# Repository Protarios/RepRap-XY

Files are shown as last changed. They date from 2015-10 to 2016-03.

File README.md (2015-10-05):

This is the first release of a RepRap-XY 3D printer. 
It is based on the great work of jand1122, which again is based on the excellent design of Zelogik. See the github archives at:  https://github.com/jand1122/RepRap-XY and https://github.com/zelogik/AluXY
I also use some of the parts parts clintonsam25 shared on the FreeCAD Forum and Github: https://github.com/clintonsam75/FreeCAD-library/tree/master/3D%20Printer and http://forum.freecadweb.org/viewtopic.php?f=24&t=6962

These designs and variants are discussed in the RepRap forum at:: http://forums.reprap.org/read.php?4,297740

jand1122 already changed the original design of zeologic so no more CNC-ed aluminium is needed. Based on this design he used printed parts instead of aluminium parts. 

The resulting design already has a great lot of features:

- Based on the Core-XY system. (see http://corexy.com/theory.html)
- Frame made from aluminium extrusions.
- No motors, belts and guides on the outside of the frame.

When thinking about the ideal FDM 3D printer I want to build those requirements come into my mind:

- Stiff Frame (check, aluminium extrusion profiles are great)
- High quality hotend (E3D or Kraken Printhead can be mounted, upgradeable)
- No Oozing Nozzle (Direct Feed or Closing Nozzle, like cel-robox has)
- Heated Bed for warp-free printing of ABS
- good first layer (automatic bed leveling, good sticking of layer to bed: Kapton Tape, PEI or GeckoTek)
- Capable of wide variety of materials
- Enclosed casing for warp and smell free printing (good starting point with jand1122's design, where no motors are outside the frame)
- Remote control with webcam support (Octopi)
- Multi Nozzle Printhead (higher printspeed, multi material / color prints)
- Swapable Head if possible

With the goal of adding such new features, like ocotopi webcam support, enclosed  caseing, dual nozzle printhead and others I decided to use jand1122s design as a basis for me own redesign.

I started with redesigning his FreeCAD parts, so screws are integrated in a nicer way and remodelling other parts in FreeCAD only available as STEP before.

Also I assemble the printer in the Freecad Assembly2 Module.

This is a work in progress, Use at your own risk.

The Folder src containes the FreeCAD files from jand1122 and from other open source 3D printer projects I used as basis for my design.

The Folder Assembly contains the FreeCAD Assembly and all Parts.
As the Assembly2 Module currently does not allow for import of subgroups of parts and the solver isn't able anymore to solve all constraints if the assembly gets to complicated I use the muxing ability of Assembly2 to join subgroups of parts, such as the XY-Slide into one part then used for further assembly in the complete product.

The file build.py will generate the STEP and STL files.
Just open the file in FreeCAD and run a a macro.

In the doc folder you will find a BOM. 
This BOM currently is fully based on jand1122's design. I will update it later.
This BOM is not generated from the model but hand made, so be carefull
You will not (yet?) find build instructions there.  Have a look at the sourcefiles RepRap-XY.FCStd (FreeCAD) to see how everything fits together.

To see some videos of jand1122's printer have a look at his youtube channel: https://www.youtube.com/channel/UCOyTdQOCCLdy45FtSlam_3A/feed
and some images at his imgur album: http://jand1122.imgur.com/

As I first want to complete the printer in CAD before I start any real life assembly it will be sone time until I can sho you videos or pictures of mine.

Have fun.

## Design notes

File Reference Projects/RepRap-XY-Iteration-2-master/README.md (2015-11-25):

# RepRap-XY-Iteration-2
## Open Source CoreXY RepRap 3D Printer
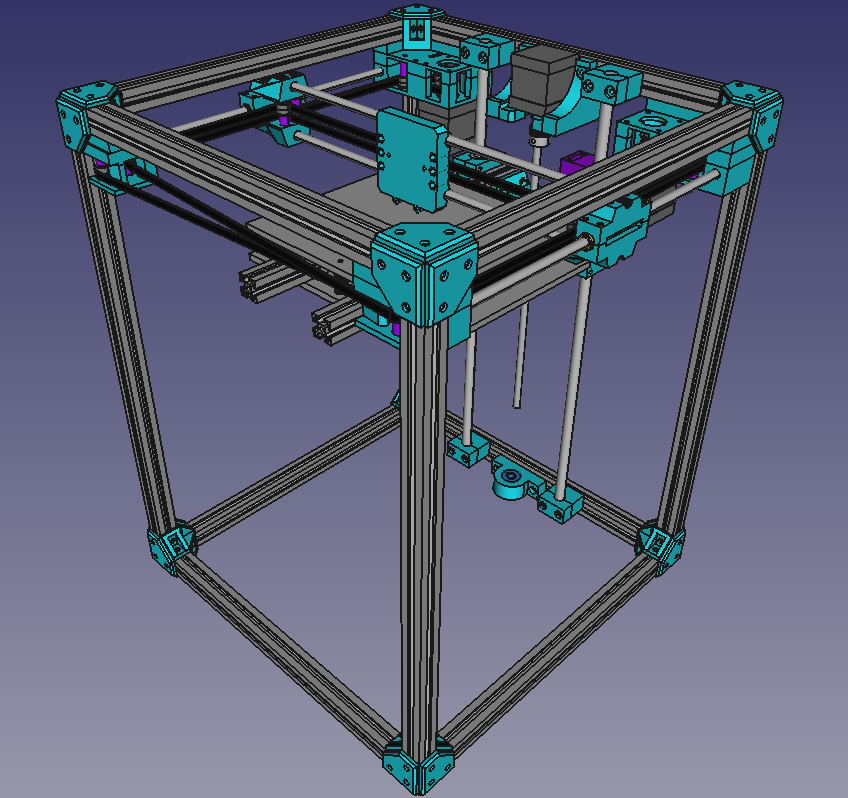
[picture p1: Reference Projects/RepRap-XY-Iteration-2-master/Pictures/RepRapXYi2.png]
RepRap-XY Iteration 2 Assembly

 RepRap-XY Iteration 2 FreeCAD Assembly

This is a modified release of the RepRap-XY 3D printer. It is based on the excellent design of Jand archive at:https://github.com/jand1122/RepRap-XY

Their designs/variants are discussed in the RepRap forum at:: http://forums.reprap.org/read.php?4,297740

RepRap-XY-Iteration 2 is designed to be an improvement over the original RepRap-XY design provided by Jand1122. Iteration 2 incorporated a modified X carriage and XY blocks from sdavi and incorporates 2020 coner brackets inspired by user ybm.

Iteration 2 Modifications:
- Sdavi's XY Blocks modified for 8x12x30 Brash Bushings
- Custom X Carriage based on Sdavi's design remodeled from scratch
- Mounting for E3D V6, E3D Chimera, E3D Cyclops 
- Increased Z axis height of 100mm, printer height 500mm
- Corner bracket parts for frame in lieu of metal right angle t-slot brackets
- Spacer corner brackets for motor blocks and idler blocks, also add structur to frame
- (x2) B'Struder Direct Driver Extruder w/ MK8 Driver Gear setup for 1.75mm Filament
- Mounting for Ultimachine RAMBo/AMBIT

## Bill of Materials

Frame
- (4x) 500mm 20x20 Length of Aluminum Extrusion
- (12x) 260mm 20x20 Length of Aluminum Extrusion
- Lots of M4 T-nuts
- (24x) Printed Corner Brackets
- (4x) Printed Inner Corner Brackets

Z Axis
- (2x) 12mm Rod 500mm
- Trapizoidal Lead Screw
- 5X10 Motor Coupler
- (2x) LM12LUU 12mm Long Linear Bearing
- Nema17 Stepper Motor
- (4x) M4 T-nuts
- (2x) 100mm 20x20 Aluminum Extrustion Length
- 14x 40mm M5 bolt
- (8x) 25mm M5 bolt
- (4x) 15mm M3 bolt (to attach nema motor)

X & Y Axis
- (2x) NEMA17 Stepper Motors
- (24x) F624ZZ flanged bearings
- (2x) 330-350mm 8mm diameter smooth rod (y-axis)
- (2x) 400mm 8mm diameter smooth rod (x-axis)
- (6x) LM8UU 8mm linear bearing
- Approx. 3-4m GT2 belt
- (2x) 20 tooth GT2 Pulley
- (4x) 60mm M4 bolts (for XY block bearings)
- (40x) M4 bolts
- (12x) 40mm M3 bolts
- (8x) 40mm M4 bolts (for idler bearings, screws can be longer)
- (8x) 25mm M5 bolts
- (6x) 55mm M5 bolts
- (4x) 30mm M5 bolts
- (6x) 15mm M3 bolt
- (8x) 10mm M3 bolt (attach nema motors)

Liscensing: 
Creative Commons Attribution-ShareAlike 4.0 International License

https://creativecommons.org/licenses/by-sa/4.0/legalcode

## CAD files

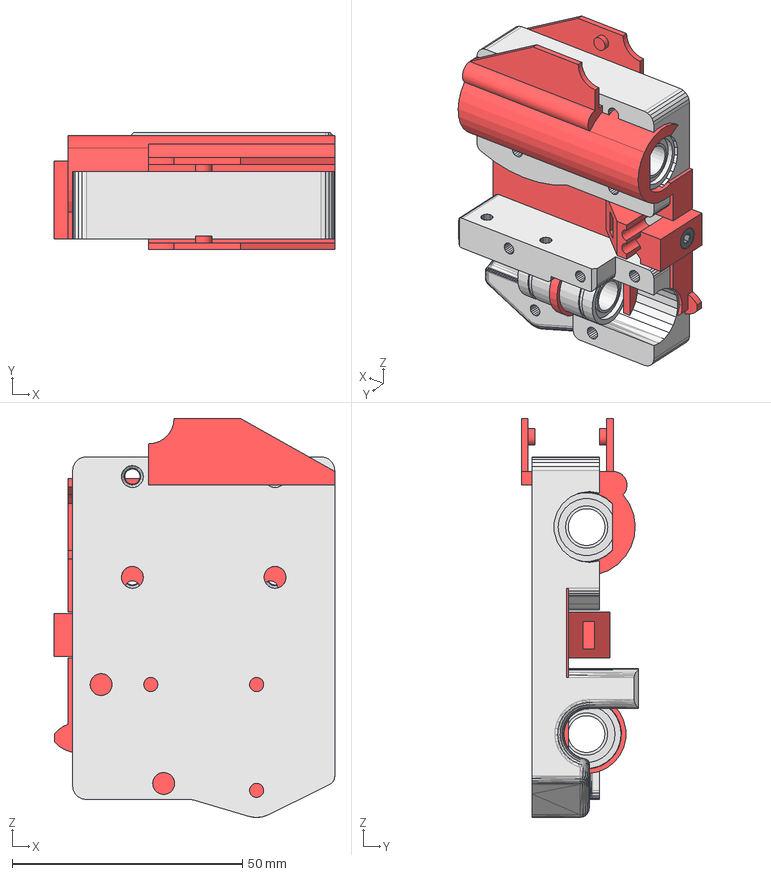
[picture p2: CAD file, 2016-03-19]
Assembly/Parts/Extruder/Toronado-Carrier-Assembly.FCStd
61.0 x 25.5 x 86.7 mm
x-carriage-final
x-LM8uu-top-1
x-LM8uu-top-002
x-LM8uu-bottom-003
x-carriage-zip-tie
x-carriage-B-final
M3-nut
M3x20-hex-bolt002
tpge_xcarriage002

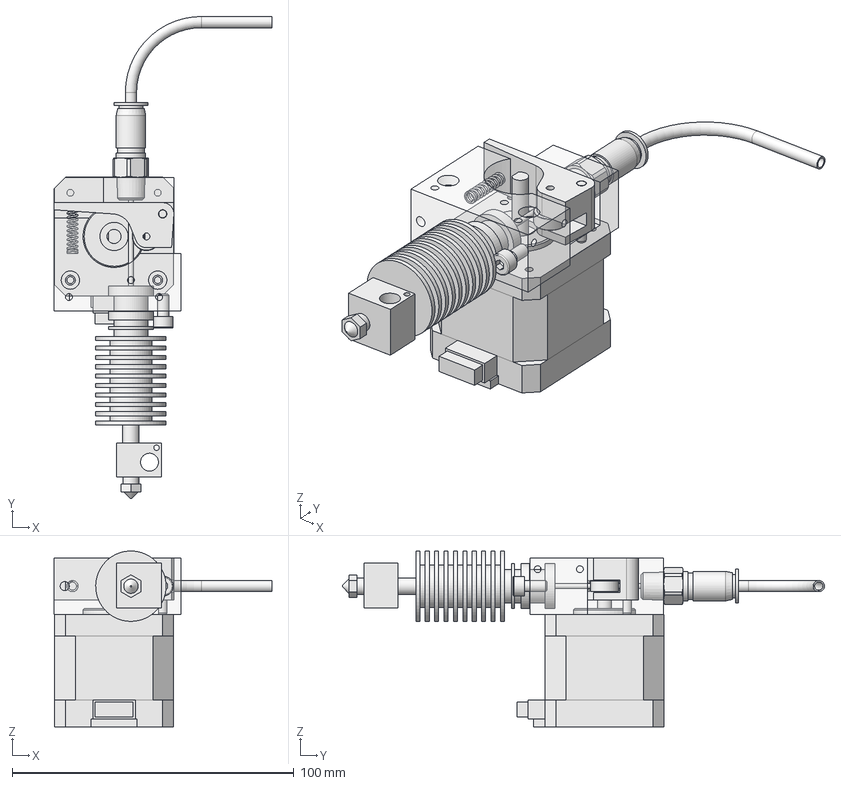
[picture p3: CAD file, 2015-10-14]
Assembly/Sub-Assemblies/extruder-assembly.FCStd
77.3 x 171.1 x 62.5 mm
C04H020019-extruder-spring
C04H030096-extruder-motor-support
C04H030009-Extruder-lever
Extruder_tube-end
C04H040001-pneumatic-fitting
C04H020008-Bearing-623zz
Extruder-body-bolt-2
hot-end-PLA-filament
C04H010011-extruder-motor
C04H050004-dowel-pin
hotend final001

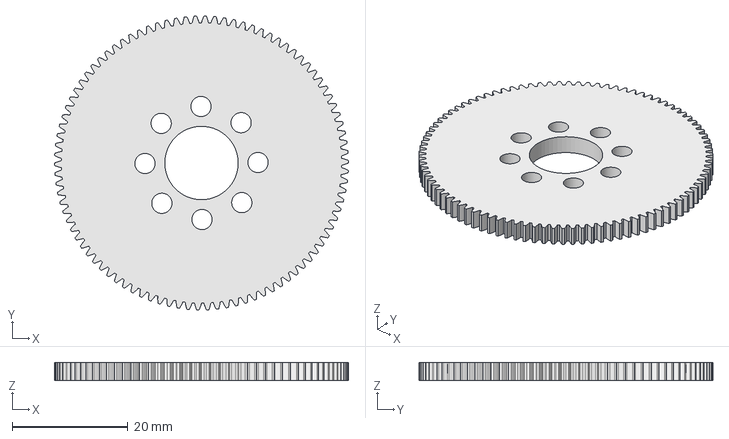
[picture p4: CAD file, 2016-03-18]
Assembly/Sub-Assemblies/Muxed Assemblies/The_Toranado_Precision_Geared_1.75mm_Extruder/files/Acetal Main Gear.FCStd
50.9 x 50.9 x 3.17 mm

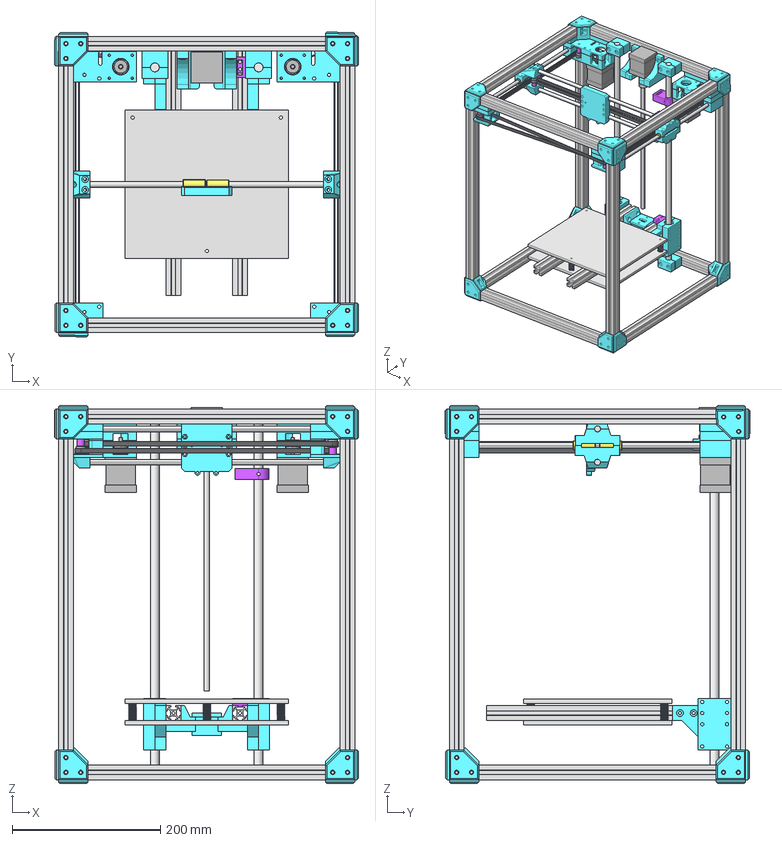
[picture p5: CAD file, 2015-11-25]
Reference Projects/RepRap-XY-Iteration-2-master/src/RepRap-XY-Iteration-2-Assembly.fcstd
410.7 x 411.3 x 510.0 mm
Nema-17
Nema-018
Nema-019
F624zz-bearing
624-bearing
spacer-1
F624zz-bearing001
624-bearing001
washer-M4
washer-M005
F624zz-bearing002
624-bearing002
washer-M006
washer-M007
F624zz-bearing003
624-bearing003
washer-M008
washer-M009
F624zz-bearing004
624-bearing004
washer-M010
washer-M011
washer-M012
washer-M013
F624zz-bearing005
624-bearing005
spacer-002
washer-M014
washer-M015
F624zz-bearing006
624-bearing006
spacer-003
washer-M016
washer-M017
F624zz-bearing007
624-bearing007
spacer-004
washer-M018
washer-M019
F624zz-bearing008
624-bearing008
washer-M020
washer-M021
F624zz-bearing009
624-bearing009
washer-M022
washer-M023
F624zz-bearing010
624-bearing010
washer-M024
washer-M025
F624zz-bearing011
624-bearing011
washer-M026
washer-M027
Alu-20x20x360
Alu-20x20x361
Alu-20x20x362
Alu-20x20x363
Alu-20x20x367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

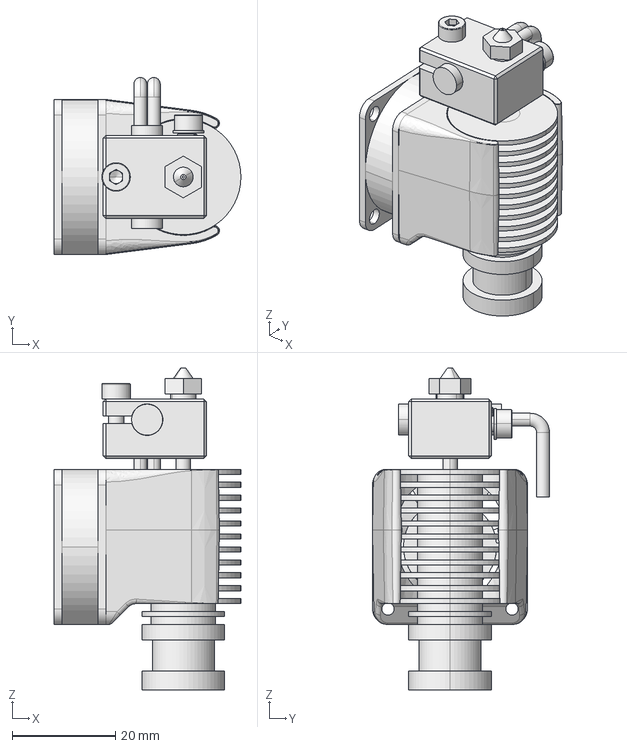
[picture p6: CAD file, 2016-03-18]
Assembly/Sub-Assemblies/Muxed Assemblies/The_Toranado_Precision_Geared_1.75mm_Extruder/files/E3D-v6_Assembly.FCStd
36.2 x 34.2 x 62.3 mm

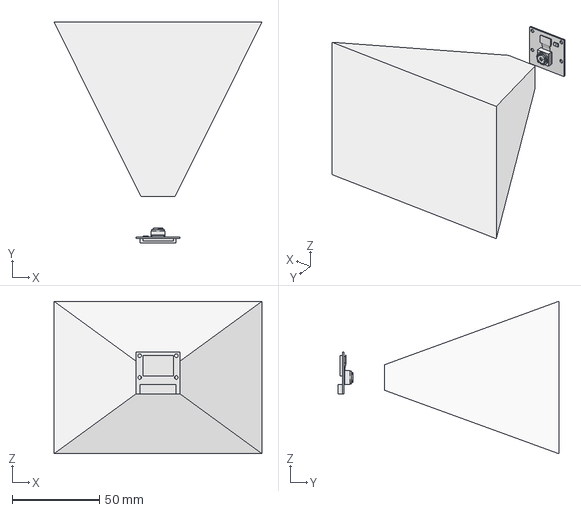
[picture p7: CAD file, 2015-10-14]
Assembly/Parts/!Temp Folder/3D Printer Parts/Pi-Camera.FCStd
119.2 x 126.5 x 87.4 mm
FOV_01

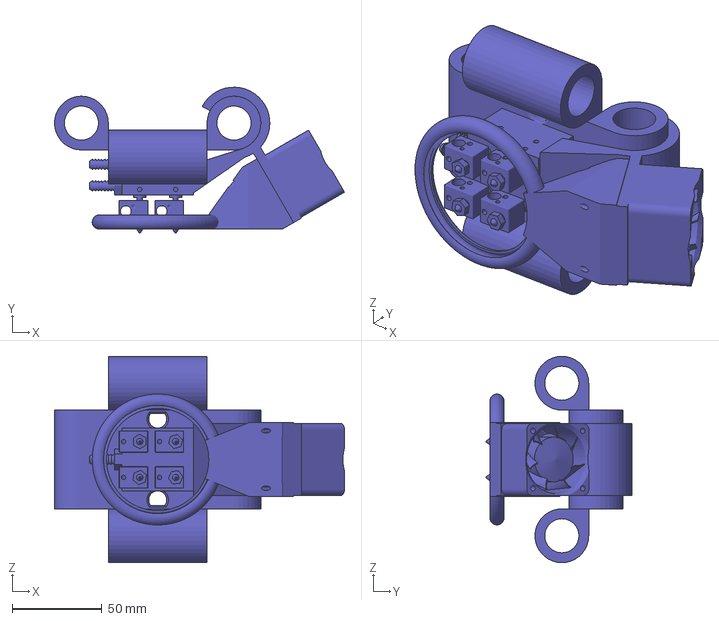
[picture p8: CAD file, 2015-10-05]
Assembly/Parts/!Temp Folder/Hotend/Kraken_stl_to_FC.FCStd
161.6 x 81.1 x 115.0 mm

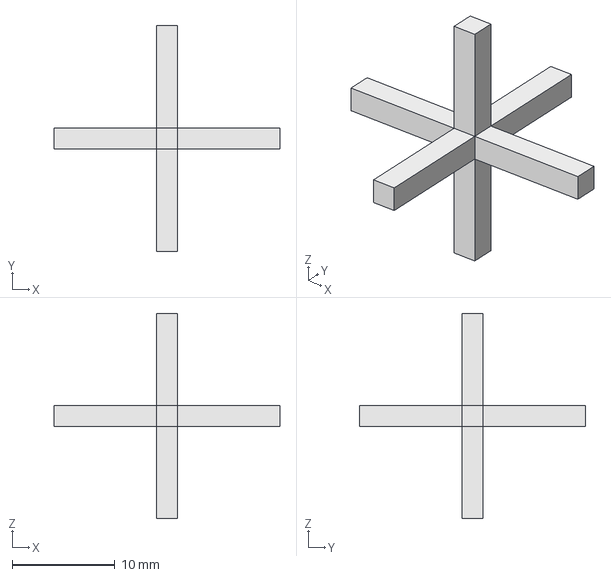
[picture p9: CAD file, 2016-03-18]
Assembly/Parts/!Temp Folder/Koordinatenkreuz.FCStd
22.0 x 22.0 x 20.0 mm

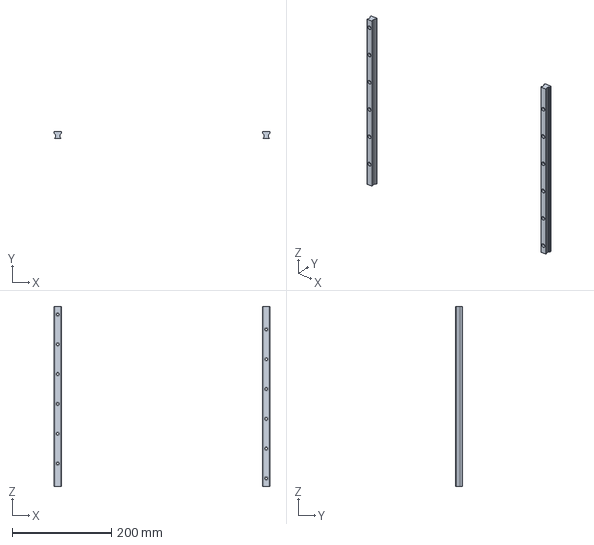
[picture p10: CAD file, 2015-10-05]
Assembly/Parts/!Temp Folder/Z/Z-Bearings.FCStd
435.0 x 15.0 x 363.0 mm

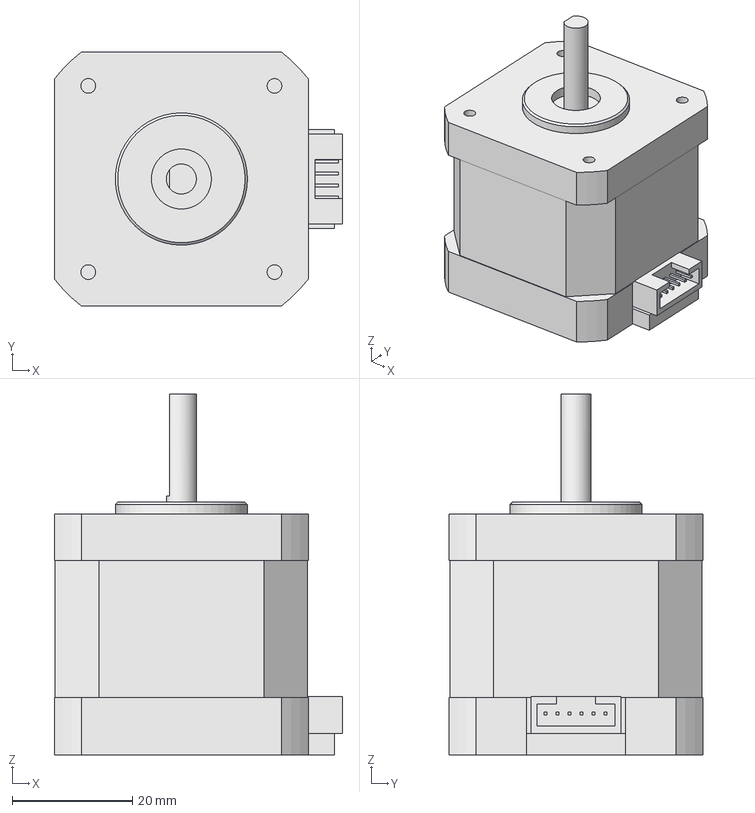
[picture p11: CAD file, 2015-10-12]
Assembly/Parts/3D Printer Components/NEMA-17_Stepper_Motor_40mm_with_connector.fcstd
48.0 x 42.3 x 60.1 mm

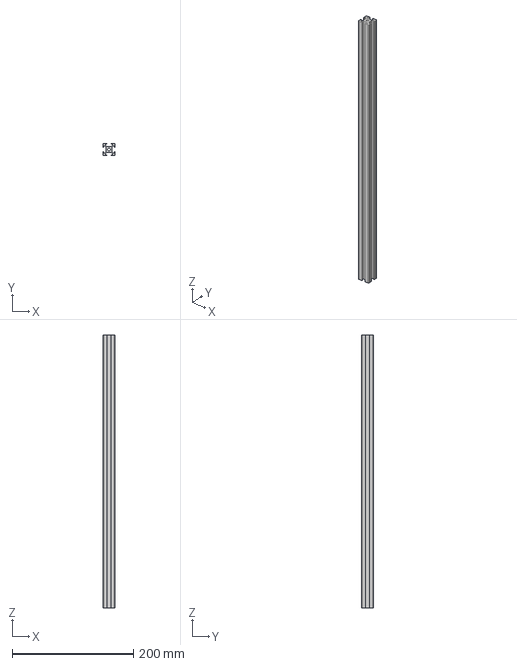
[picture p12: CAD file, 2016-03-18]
Assembly/Parts/Alu Extrusion/tslot20x20x450.FCStd
20.0 x 20.0 x 450.0 mm

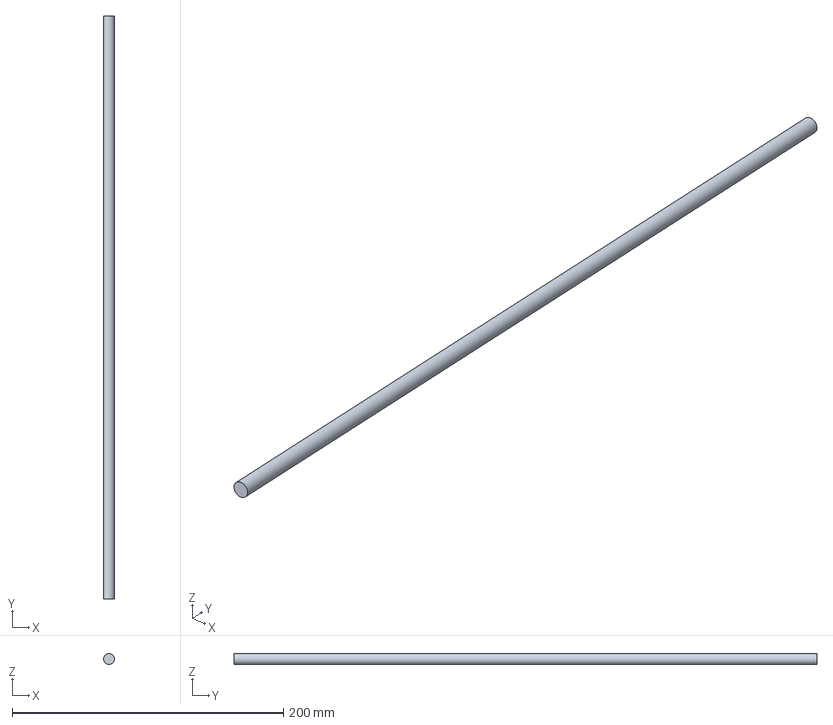
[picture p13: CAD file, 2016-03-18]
Assembly/Parts/Bearings/smooth-bar-8x430.FCStd
7.99 x 430.0 x 8.00 mm

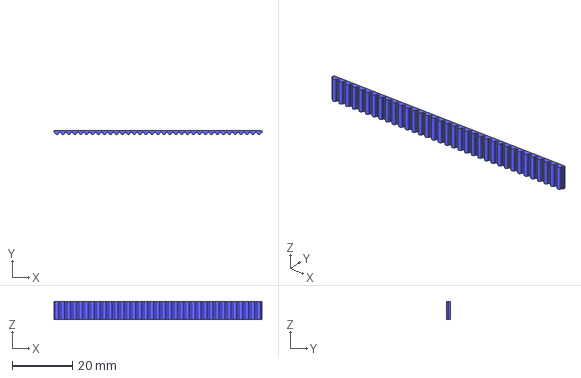
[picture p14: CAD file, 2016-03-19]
Assembly/Parts/Belts/Beltpiece.step
69.3 x 1.38 x 6.00 mm

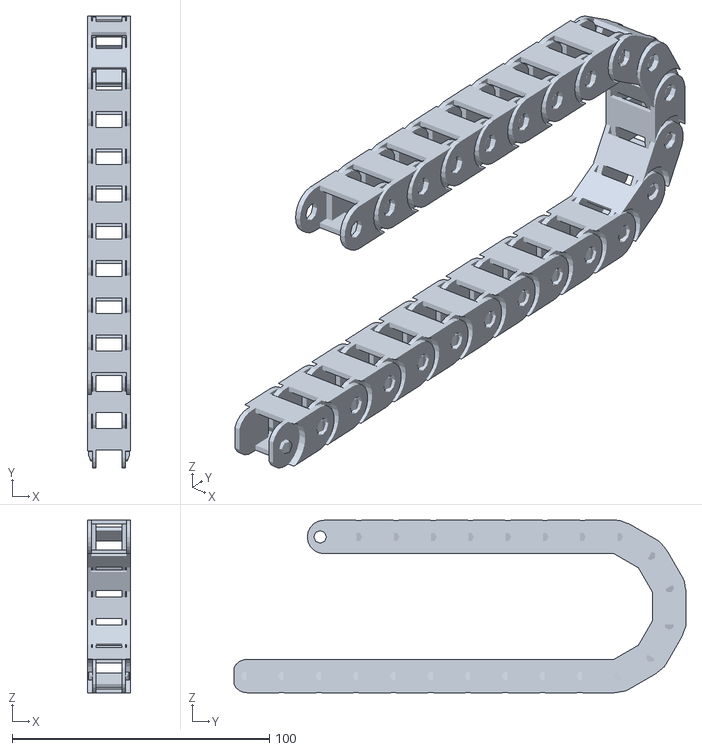
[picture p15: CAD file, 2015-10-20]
Assembly/Parts/Cable Chain/Parametric OPENSCAD Cable Chain/ParametricCableChain.stl
16.6 x 175.8 x 67.1

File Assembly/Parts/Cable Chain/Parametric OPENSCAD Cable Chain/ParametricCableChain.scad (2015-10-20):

//
// PARAMETRIC Cable Chain v0.5
// Zerginator 10/2015
//

// - changes V1.2:
//  - added missing grip-size modifiers
//
// - changes V1.1:
//  - added variable hinge length:
//    "hiHeight" now specifies the height of the hinge pin, relative to the bottom.

use <text_on.scad>


chainlength = 30;
//ChainDef = [[1,10],[1,0],[1,0],[1,0],[1,0],[1,0],[1,0],[1,0],[1,0],[1,0],[1,30],[1,30],[1,30],[1,30],[1,30],[1,30],[1,0],[1,0],[1,0],[1,0],[1,0],[1,0],[1,10]];

ChainDef = [[1,10],[1,0]];

PrintIT     =       0;          // Remove all Angles, so it can be printed
BedSize     =       100;        // Longest Printbed Size (printable area), so chain is automatically split for printing
Override    =       0;          // Override Idiot Cube Warning

//$fs=0.5;
//$fa=0.5;

// ===============================================================================
// Type
Type        =       2;         // 1: +45° Bewegbar, 2: +-45°, Adapter auf Frei, Adapter Richtungswechsel
//der aktuelle typ ist der -45° Typ-> also nr. 3!
Round       =       1;         // Runder oder eckiger Typ
// Unterteilung von breiten Cable Chains
// RepRap Industrial Type Chain
// Enden: http://www.thingiverse.com/thing:11978/#files
// open Cable Chain http://www.thingiverse.com/thing:611593
// mit filament zur unterteileung
//  eiPionezero Chain http://www.thingiverse.com/thing:666118/#remixes / Enden: http://www.thingiverse.com/thing:876092
// mit Loch http://www.thingiverse.com/thing:926073
// Divider Insert: http://www.thingiverse.com/thing:786581
// Aufklipps Ecke ist noch fehlerhaft bei großer Höhe, genauso wie Eckausschnitt

ChainP      =       0;          // Chainprintable
Start       =       0;          // -45°
End         =       0;          // +-45°
Open        =       0;          // Open / Closed / Closed with Filament / Closed with 2 Filaments
PrintCl     =       1;          // Print Closing Element
Tolerance   =       0;
space       =       0.3;        // Space between the chain parts and the matches - 0.2
anglerest       =      90;          // anglerest for maximum bending of one peace. -  45 // Possible values from 0 - 90
overlapping =       0.01;       // overlapping value to make the Object simple - leave this at 0.01
conntweak   =       0;          // Connection tweak - 0 - You may add or subtract here a little for the nopples, so the whole thing gets stickier or less between the chainparts.



// ===============================================================================
// box parameters
width       =       45;       // length of the box (Standard: 16.6)
height      =      20;         // width of the box (Standard: 13)
length      =       35;         // height of the lid  (Standard: 25, min 30 für Eckig)
wall        =       1.2;        // Wall thinkness - 1.2


// ===============================================================================
// === OUTPUT


// ===Check Consistency of Values
if((!Type && !Start && !End) || ((Round != 1) && (length/height<2.2)))
{
    // === IDIOT BOX (if imposible values were selected)
    cube([30,30,30]);
    color("red")
    text_on_cube("Doh!!", locn_vec=[15,15,15], cube_size=30, face="top", size=5, center=true); 
    color("red")
    text_on_cube("Error!!", locn_vec=[15,15,15], cube_size=30, face="front", size=5, center=true);   
    color("red")
    text_on_cube("Fehler!!", locn_vec=[15,15,15], cube_size=30, face="right", size=4, center=true);   
    color("red")
    text_on_cube("Défaut!!", locn_vec=[15,15,15], cube_size=30, face="left", size=4, center=true);   
    color("red")
    text_on_cube("ошибка!!", locn_vec=[15,15,15], cube_size=30, face="back", size=4, center=true); 
    color("red")
    text_on_cube("错误!!", locn_vec=[15,15,15], cube_size=30, face="bottom", size=4, center=true);     
}

else
// === Put the Parts together to a single Chain object
// === Magic happens here, make several chain parts and add them to a chain
{
    if( Round == 1)
    {
        vec = select2(ChainDef,[1]);
        for (i = [1:len(ChainDef)]) { 
            c = sumv(vec,i-1,0);
            a = coslength(i,ChainDef,vec); //c-ChainDef[i-1][1]
            b = sinlength(i,ChainDef,vec); //(sin(ChainDef[i-1][1]));
           echo(i,c,c-ChainDef[i-1][1],b);
//            echo(((height/13)*(length-10.5))*(sin(ChainDef[i-1][1])));
            pcsOChain(width, length, height, wall,anglerest, 0, a, b, c);
        }
    }


    if( Round != 1)
    {
        for (i = [0:len(ChainDef)-1]) { 
            pcsOChain(width, length, height, wall,anglerest, 0, i * (length - height), 0, 30);
        }
    }
}


// ===============================================================================
// === Mathematikfunktionen
function sumv(v,i,s=0) = (i==s ? v[i] : v[i] + sumv(v,i-1,s));
function select(source_vector,select_vector)=
   [ for (i = [0 : len(select_vector) - 1]) source_vector[select_vector[i]] ];
function select2(source_vector,select_vector)=
   [ for (i = [0 : len(source_vector) - 1]) source_vector[i][1] ];
function coslength(j,ChainDef,vec,s=1)=
   (j==s ? (((height/13)*(length-10.5)) * cos(sumv(vec,j-1,0)-ChainDef[j-1][1])) : (((height/13)*(length-10.5))) * cos(sumv(vec,j-1,0)-ChainDef[j-1][1]) + coslength(j-1,ChainDef,vec));  
   
function sinlength(j,ChainDef,vec,s=1)=
   (j==s ? ((height/13)*(length-10.5))*(sin(sumv(vec,j-1,0)-ChainDef[j-1][1])) : ((height/13)*(length-10.5))*(sin(sumv(vec,j-1,0)-ChainDef[j-1][1])) + sinlength(j-1,ChainDef,vec));


// ===============================================================================
// === Generate Chain module
module pcsOChain(width, length, height, wall, anglerest, posx,posy,posz, ChainAngle) 
    {    
        translate([posx,posy,posz])
        translate([0,(height/13)*4.5,(height/13)*6.5])  
        rotate(a=ChainAngle, v=[1,0,0])
        translate([0,-(height/13)*4.5,-(height/13)*6.5])  
        if (Round != 1)
        {
            pcsMiddlePart(width, length, height, wall);
            pcsOFront(width, length, height, wall,anglerest);
            translate([0,length - height - overlapping,0]) pcsOBack(width, length, height, wall);
        }
        else
        {
            CableChain(width, length, height, wall);
        }
    }





// ===============================================================================
// ===============================================================================
// ===============================================================================




// ===============================================================================
// === Cable Chain (Rund)

module CableChain(width, length, height, wall)
{
translate([width,0,0])
rotate(a=90, v=[0,0,1])
difference()
    {
    union()
        {
        difference()
            {
                union()
                   {
                    translate([0,0.1,0])
                        rotate(a=0, v=[0,0,1])
                            cube([(height/13)*(length-7.5),width,(height/13)*13]);
                    translate([(height/13)*(length-7.5),0.1,(height/13)*6.5])
                        rotate(a=90, v=[-1,0,0])
                            cylinder(r=(height/13)*6.5, h=width);
                   }
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

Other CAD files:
Assembly/Parts/Cable Chain/XY-Chain.FCStd
Assembly/Parts/Case/Subfloor.FCStd
Assembly/Parts/Electronics/MK3-300x200b.FCStd
Assembly/Parts/Frame sortieren/Torx-M8x25.FCStd
Assembly/Parts/Cable Chain/Parametric OPENSCAD Cable Chain/XY-Chain.scad
Reference Projects/RepRap-XY-Iteration-2-master/src/scad/configuration.scad
Assembly/Parts/Cable Chain/Parametric OPENSCAD Cable Chain/text_on.scad
Archive/Assembly/XY-Motor mounted below/XY-block wide.FCStd
Archive/Assembly/XY-Motor mounted below/XY-block-top wide.FCStd
Archive/Assembly/XY-Motor mounted below/XY-block-top.FCStd
Archive/Assembly/XY-Motor mounted below/XY-block.FCStd
Archive/Assembly/XY-Motor mounted below/idler-block-bottomM.FCStd
Archive/Assembly/XY-Motor mounted below/idler-block-mirrored-bottomM.FCStd
Archive/Assembly/XY-Motor mounted below/idler-block-top-bottomM.FCStd
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

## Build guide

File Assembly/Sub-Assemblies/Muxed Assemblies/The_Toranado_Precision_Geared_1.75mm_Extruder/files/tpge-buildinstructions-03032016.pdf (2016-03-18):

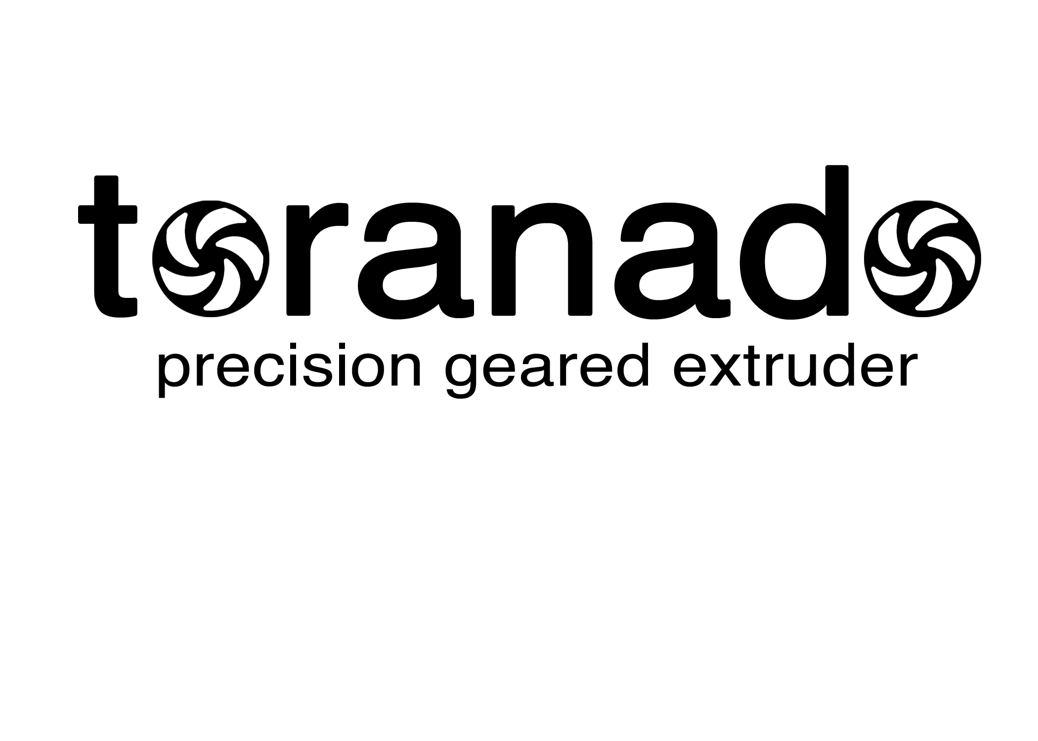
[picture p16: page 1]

2

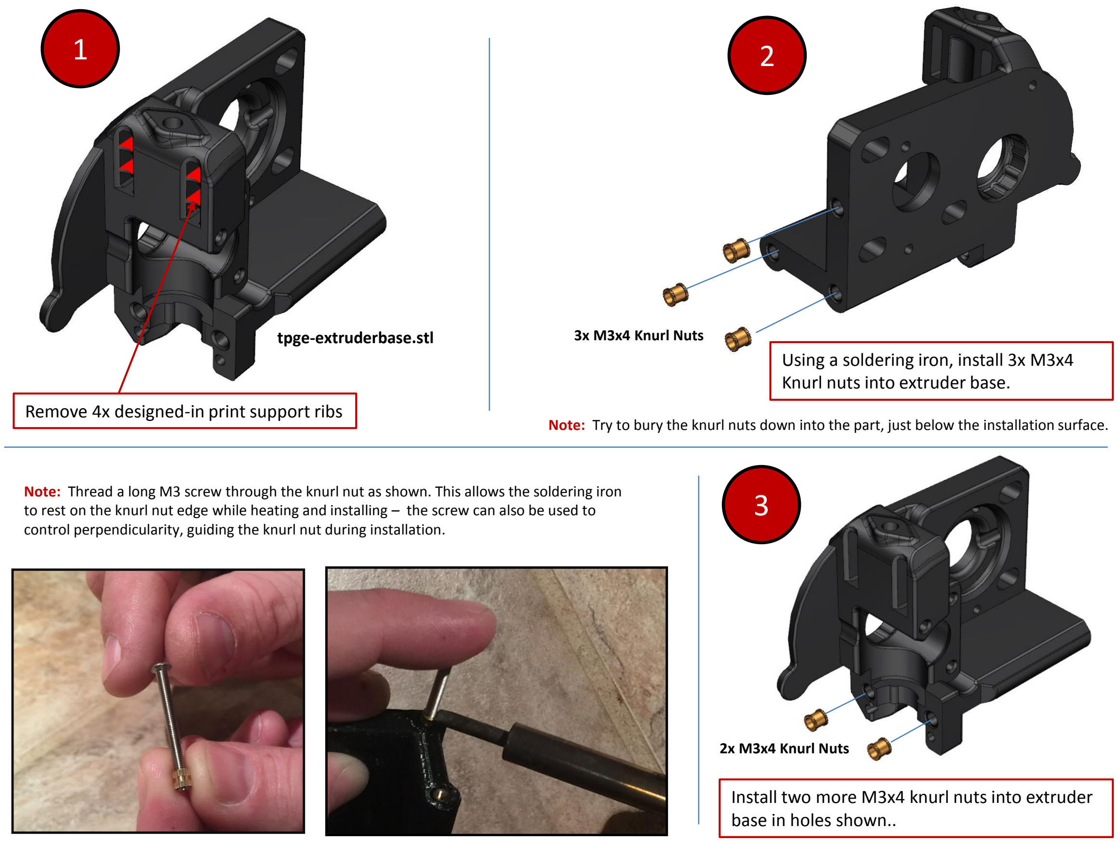
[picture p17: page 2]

### Remove 4x designed-in print support ribs

tpge-extruderbase.stl

### Using a soldering iron, install 3x M3x4

Knurl nuts into extruder base.

Note: Thread a long M3 screw through the knurl nut as shown. This allows the soldering iron to rest on the knurl nut edge while heating and installing – the screw can also be used to control perpendicularity, guiding the knurl nut during installation.

Note: Try to bury the knurl nuts down into the part, just below the installation surface.

3

### Install two more M3x4 knurl nuts into extruder

base in holes shown..

3x M3x4 Knurl Nuts

2x M3x4 Knurl Nuts

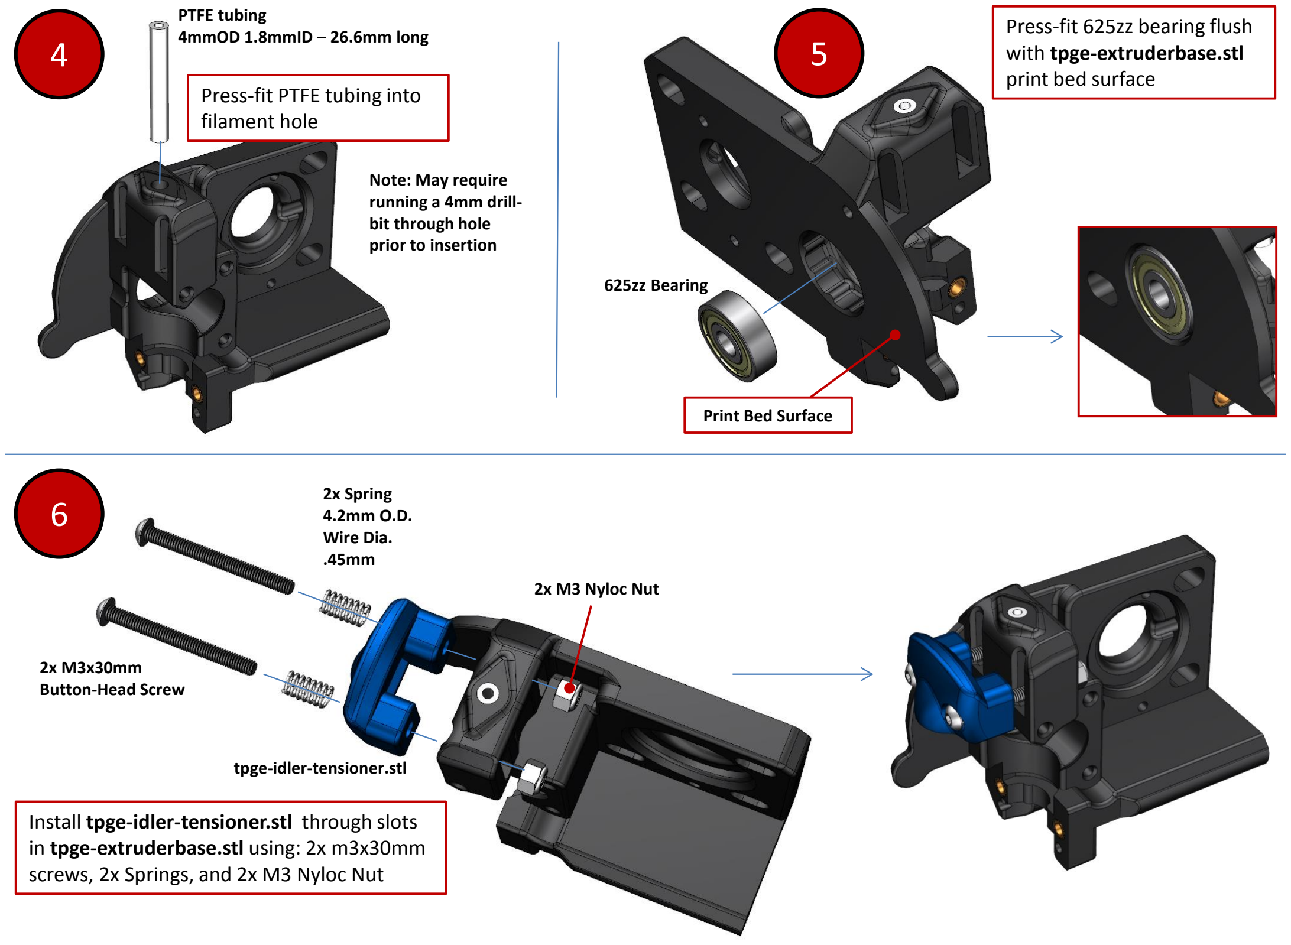
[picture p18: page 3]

### Press-fit PTFE tubing into filament hole

PTFE tubing
4mmOD 1.8mmID – 26.6mm long

Note: May require
running a 4mm drillbit through hole
prior to insertion

625zz Bearing

### Press-fit 625zz bearing flush with tpge-extruderbase.stl print bed surface

Print Bed Surface

6

2x M3x30mm
Button-Head Screw

2x Spring
4.2mm O.D.
Wire Dia.
.45mm

tpge-idler-tensioner.stl

2x M3 Nyloc Nut

### Install tpge-idler-tensioner.stl through slots in tpge-extruderbase.stl using: 2x m3x30mm screws, 2x Springs, and 2x M3 Nyloc Nut

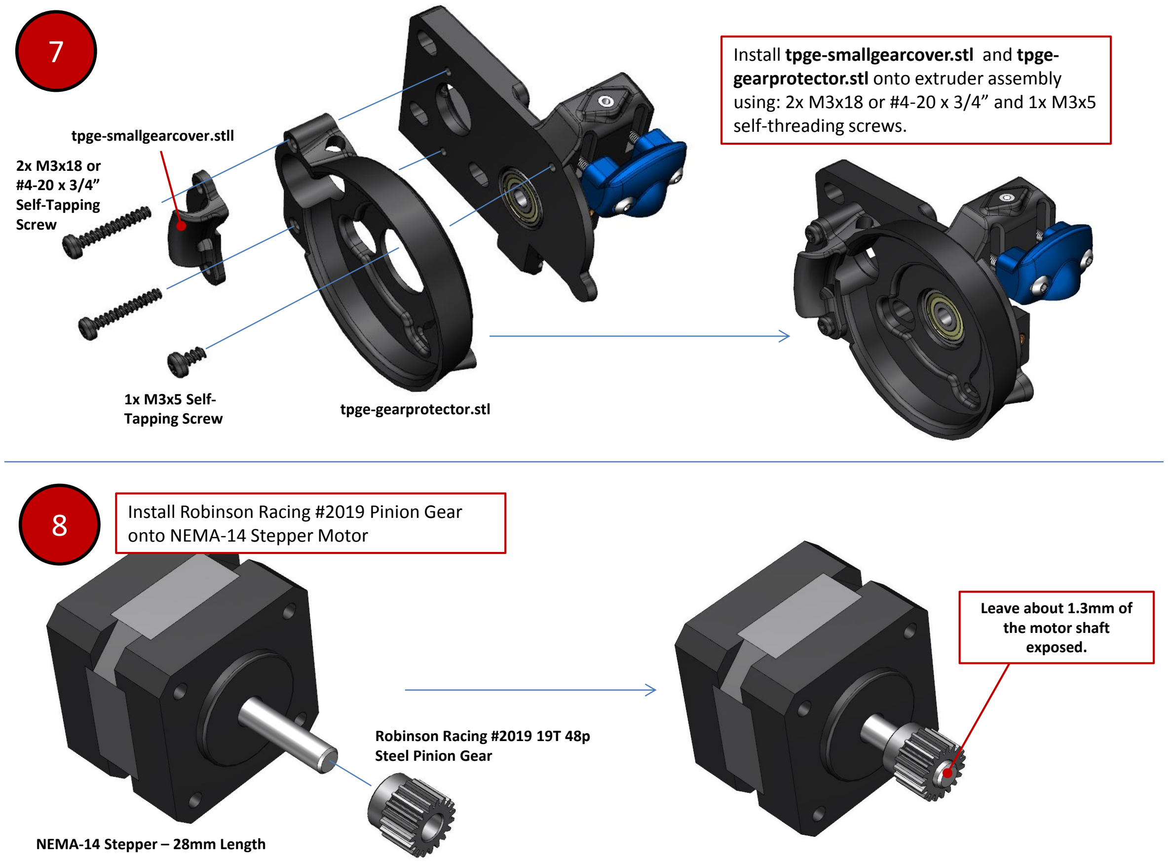
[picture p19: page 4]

7 | Install tpge-smallgearcover.stl and tpge-
| gearprotector.stl onto extruder assembly using: 2x M3x18 or #4-20 x 3/4” and 1x M3x5 self-threading screws.

2x M3x18 or
#4-20 x 3/4”

Self-Tapping
Screw

1x M3x5 Self-
Tapping Screw | tpge-gearprotector.stl

tpge-smallgearcover.stll

Install Robinson Racing #2019 Pinion Gear 8 | onto NEMA-14 Stepper Motor

NEMA-14 Stepper – 28mm Length

Robinson Racing #2019 19T 48p Steel Pinion Gear

Leave about 1.3mm of
the motor shaft
exposed.

9

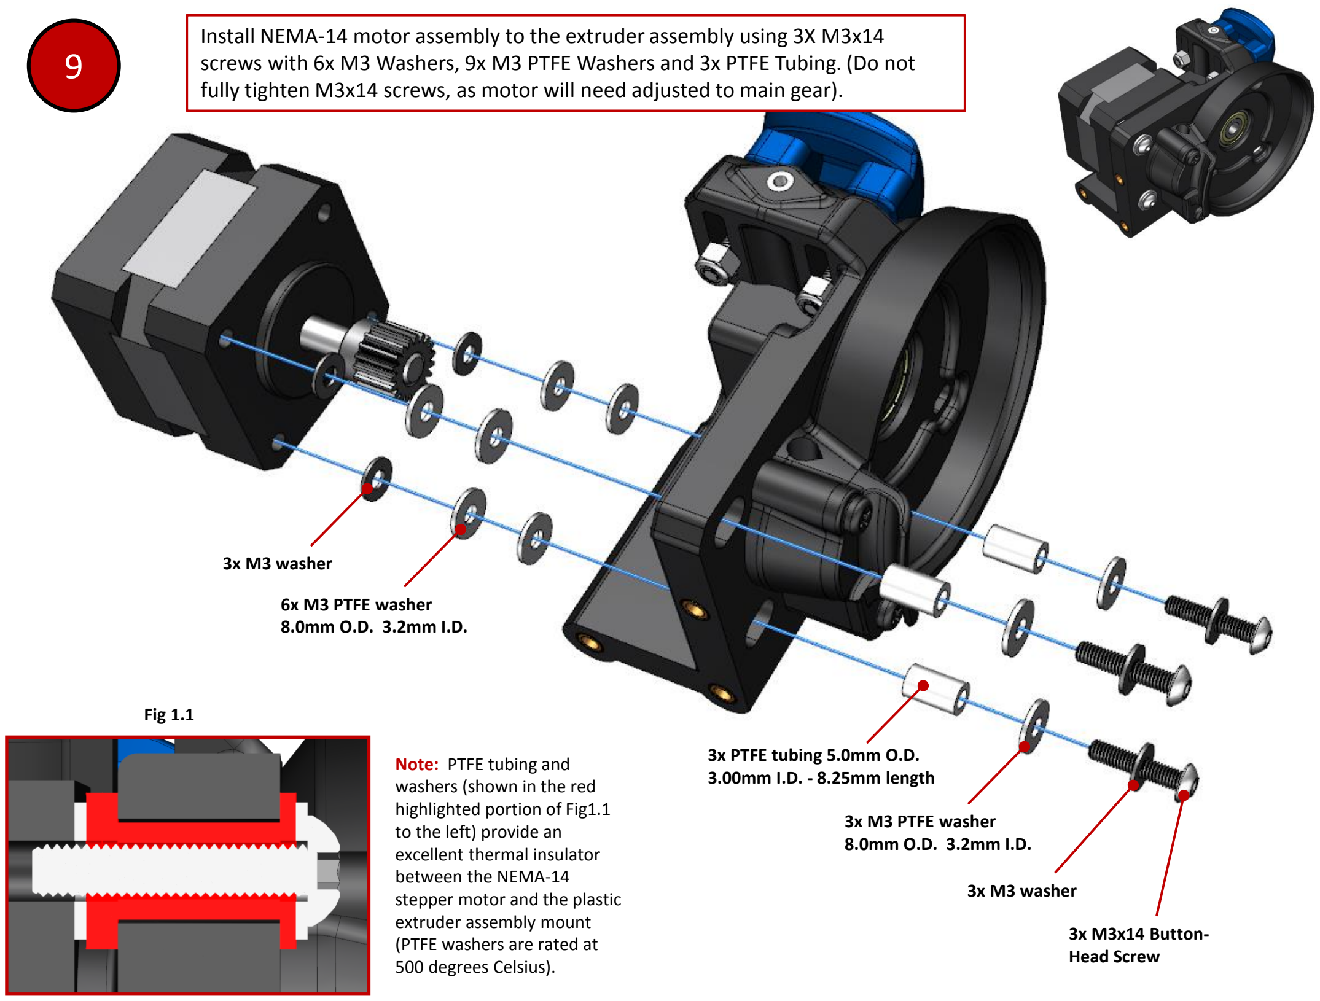
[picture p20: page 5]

### Install NEMA-14 motor assembly to the extruder assembly using 3X M3x14 screws with 6x M3 Washers, 9x M3 PTFE Washers and 3x PTFE Tubing. (Do not

fully tighten M3x14 screws, as motor will need adjusted to main gear).

3x M3 washer

6x M3 PTFE washer
8.0mm O.D. 3.2mm I.D.

3x PTFE tubing 5.0mm O.D.
3.00mm I.D. - 8.25mm length

3x M3 PTFE washer
8.0mm O.D. 3.2mm I.D.

3x M3 washer

3x M3x14 Button-Head Screw

Note: PTFE tubing and
washers (shown in the red
highlighted portion of Fig1.1 to the left) provide an
excellent thermal insulator between the NEMA-14
stepper motor and the plastic extruder assembly mount
(PTFE washers are rated at 500 degrees Celsius).

Fig 1.1

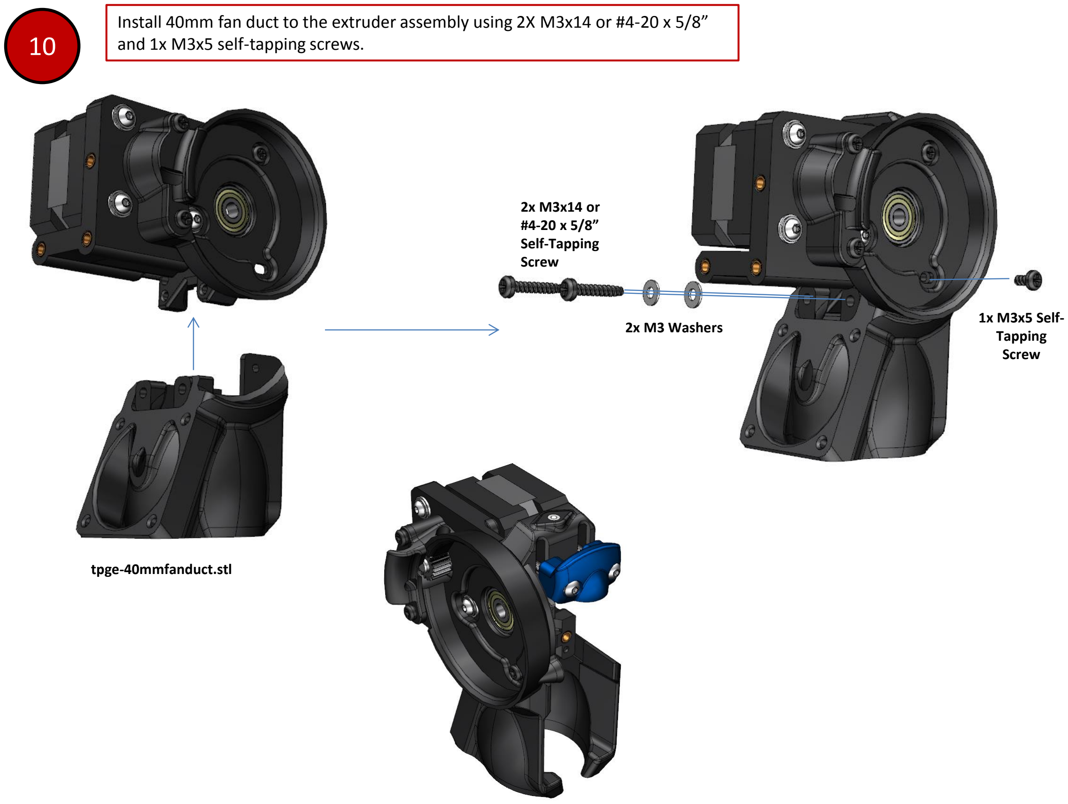
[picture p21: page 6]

### Install 40mm fan duct to the extruder assembly using 2X M3x14 or #4-20 x 5/8”

and 1x M3x5 self-tapping screws.

tpge-40mmfanduct.stl

2x M3x14 or
#4-20 x 5/8”

Self-Tapping
Screw

1x M3x5 Self-Tapping
Screw

2x M3 Washers

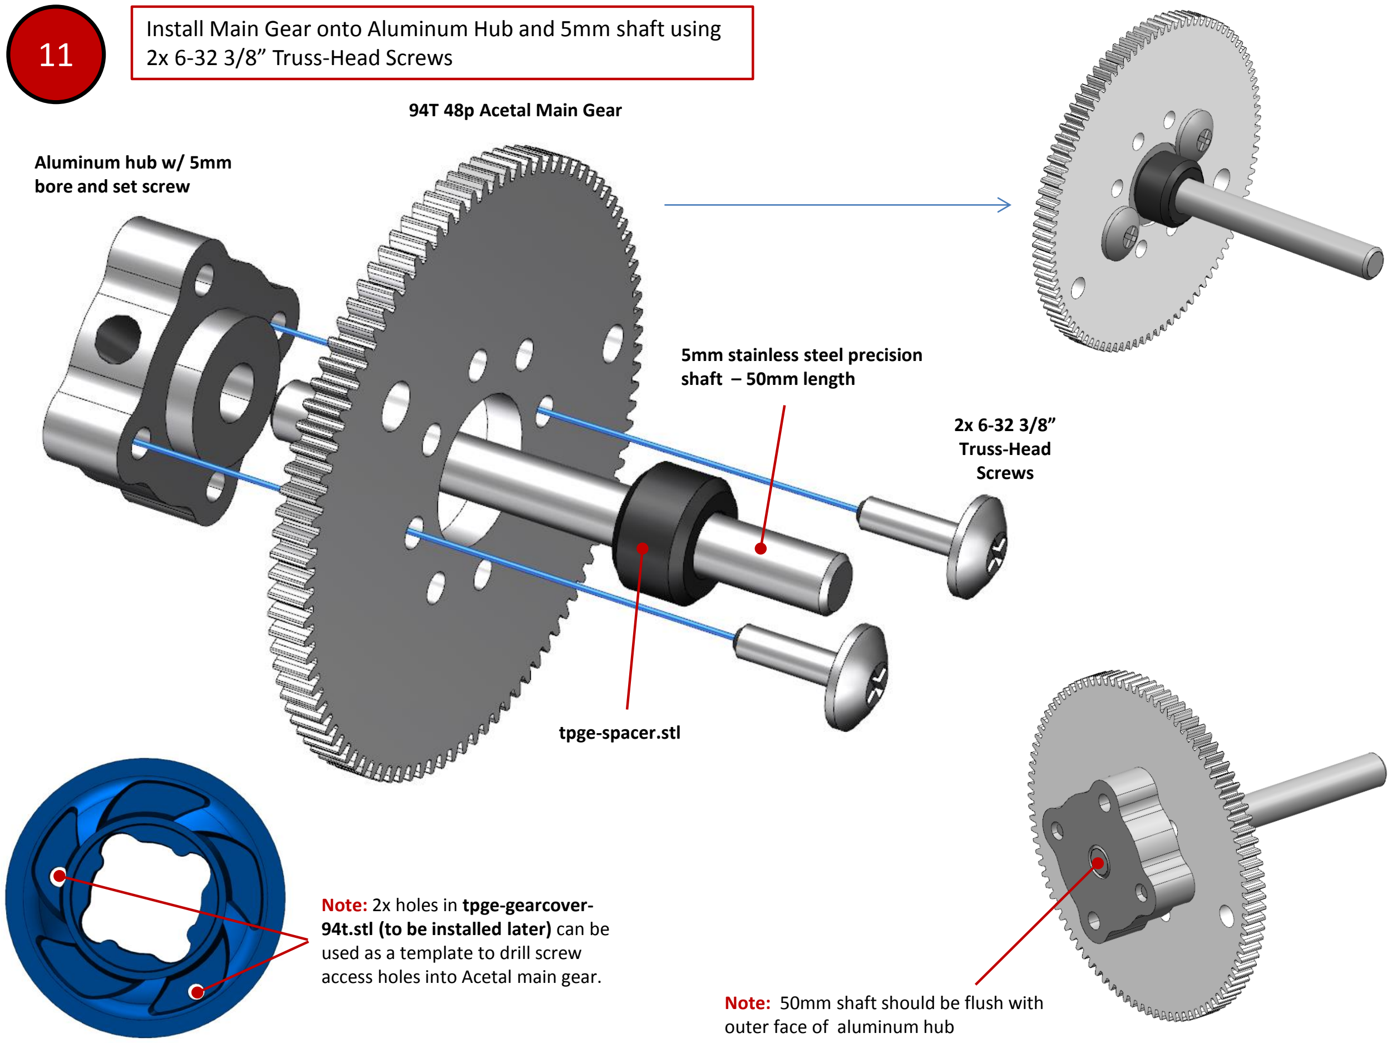
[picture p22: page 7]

### Install Main Gear onto Aluminum Hub and 5mm shaft using 2x 6-32 3/8” Truss-Head Screws

Aluminum hub w/ 5mm
bore and set screw

94T 48p Acetal Main Gear

2x 6-32 3/8”
Truss-Head
Screws

tpge-spacer.stl

5mm stainless steel precision shaft – 50mm length

Note: 50mm shaft should be flush with outer face of aluminum hub

Note: 2x holes in tpge-gearcover-94t.stl (to be installed later) can be used as a template to drill screw access holes into Acetal main gear.

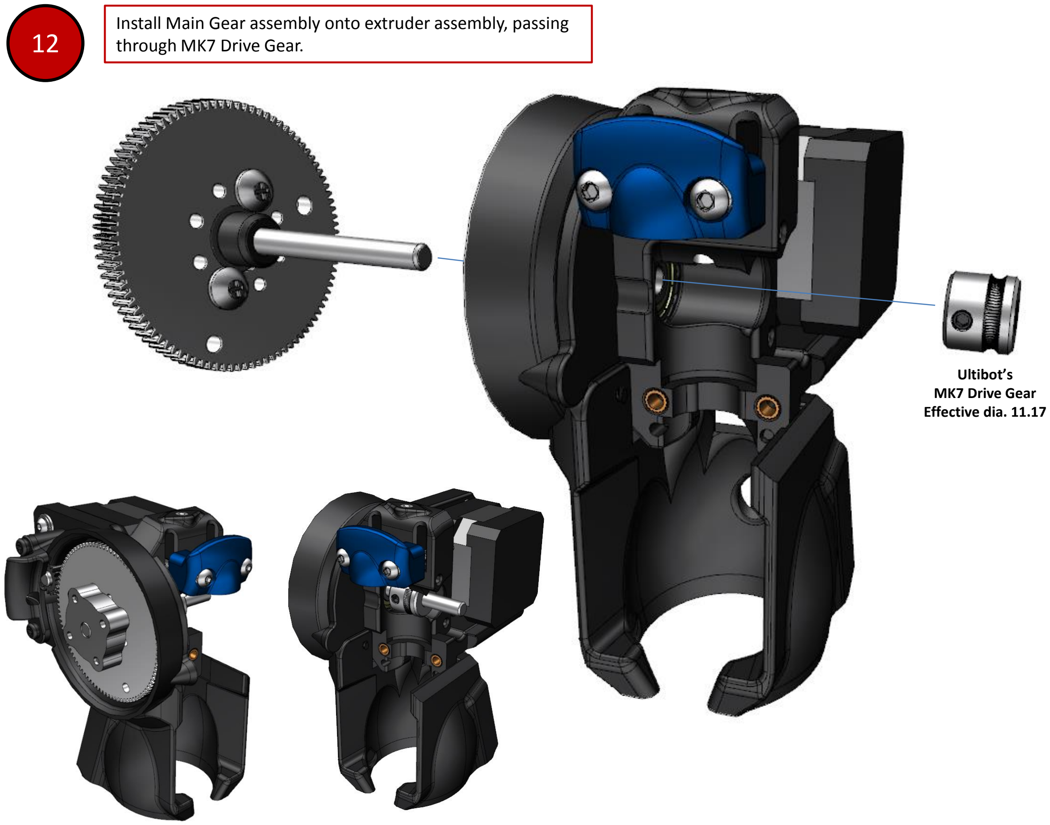
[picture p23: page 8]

### Install Main Gear assembly onto extruder assembly, passing

through MK7 Drive Gear.

Ultibot’s
MK7 Drive Gear
Effective dia. 11.17

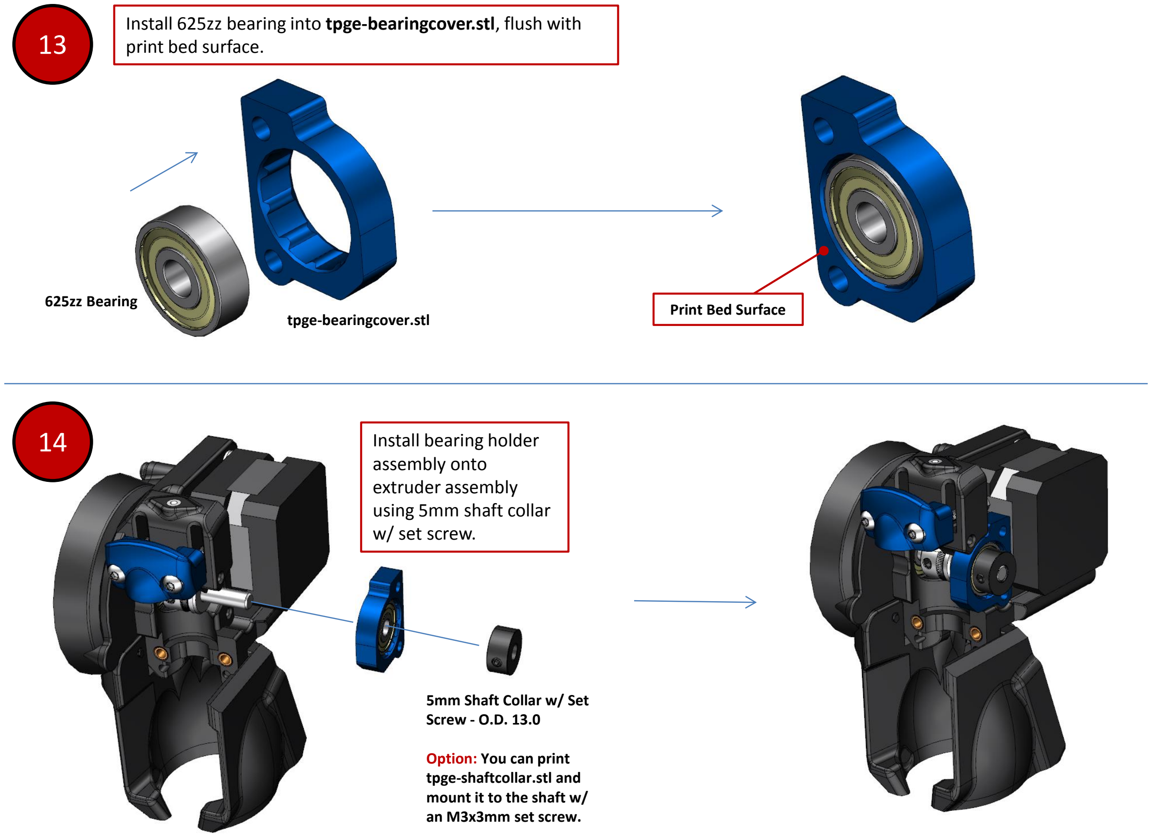
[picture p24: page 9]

### Install 625zz bearing into tpge-bearingcover.stl, flush with

print bed surface.

625zz Bearing
tpge-bearingcover.stl | Print Bed Surface
14 | Install bearing holder assembly onto extruder assembly using 5mm shaft collar w/ set screw.

5mm Shaft Collar w/ Set
Screw - O.D. 13.0

Option: You can print
tpge-shaftcollar.stl and
mount it to the shaft w/
an M3x3mm set screw.

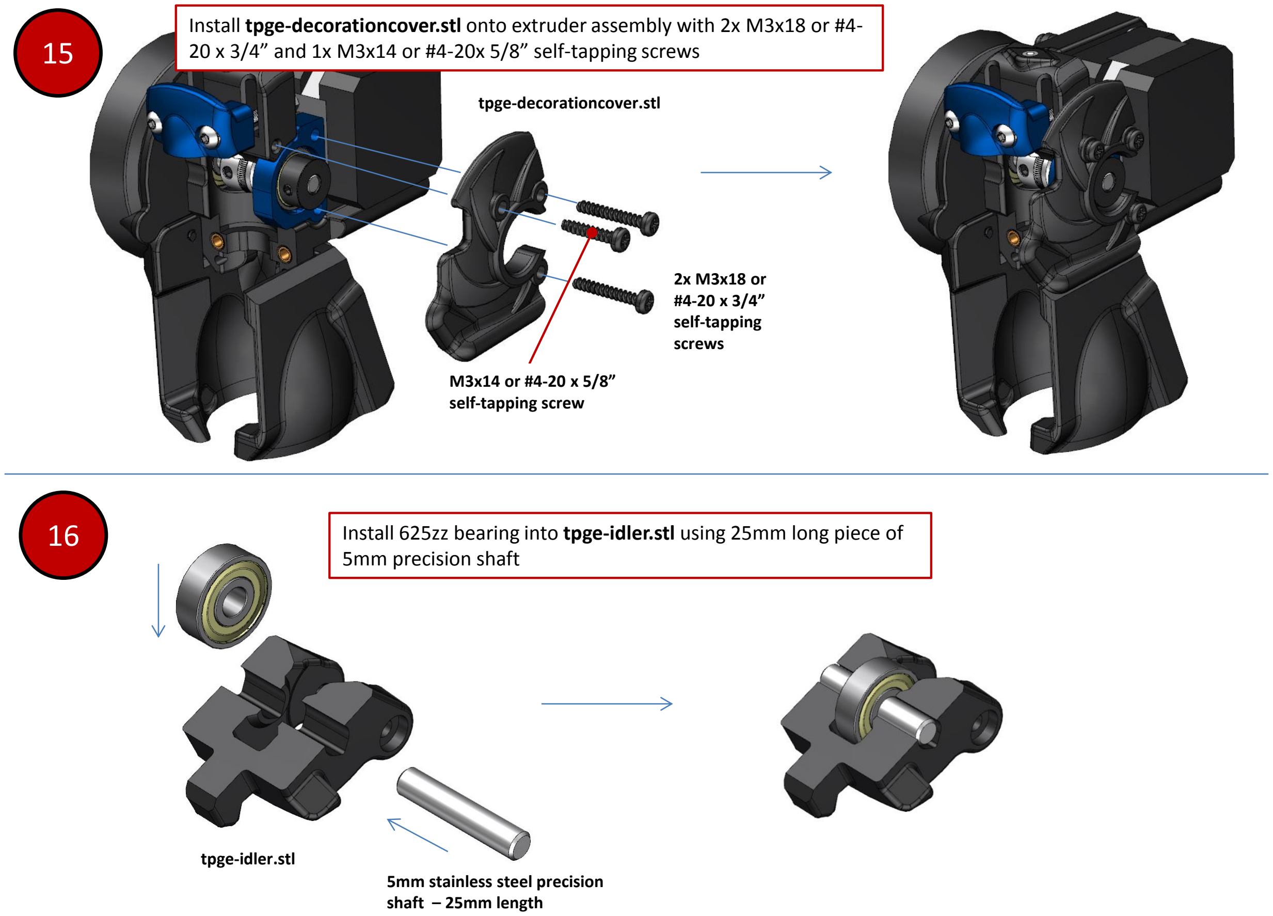
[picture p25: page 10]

2x M3x18 or
#4-20 x 3/4”

self-tapping
screws

tpge-decorationcover.stl

M3x14 or #4-20 x 5/8”
self-tapping screw

16

tpge-idler.stl
5mm stainless steel precision shaft – 25mm length

### Install tpge-decorationcover.stl onto extruder assembly with 2x M3x18 or #4-20 x 3/4” and 1x M3x14 or #4-20x 5/8” self-tapping screws

### Install 625zz bearing into tpge-idler.stl using 25mm long piece of 5mm precision shaft

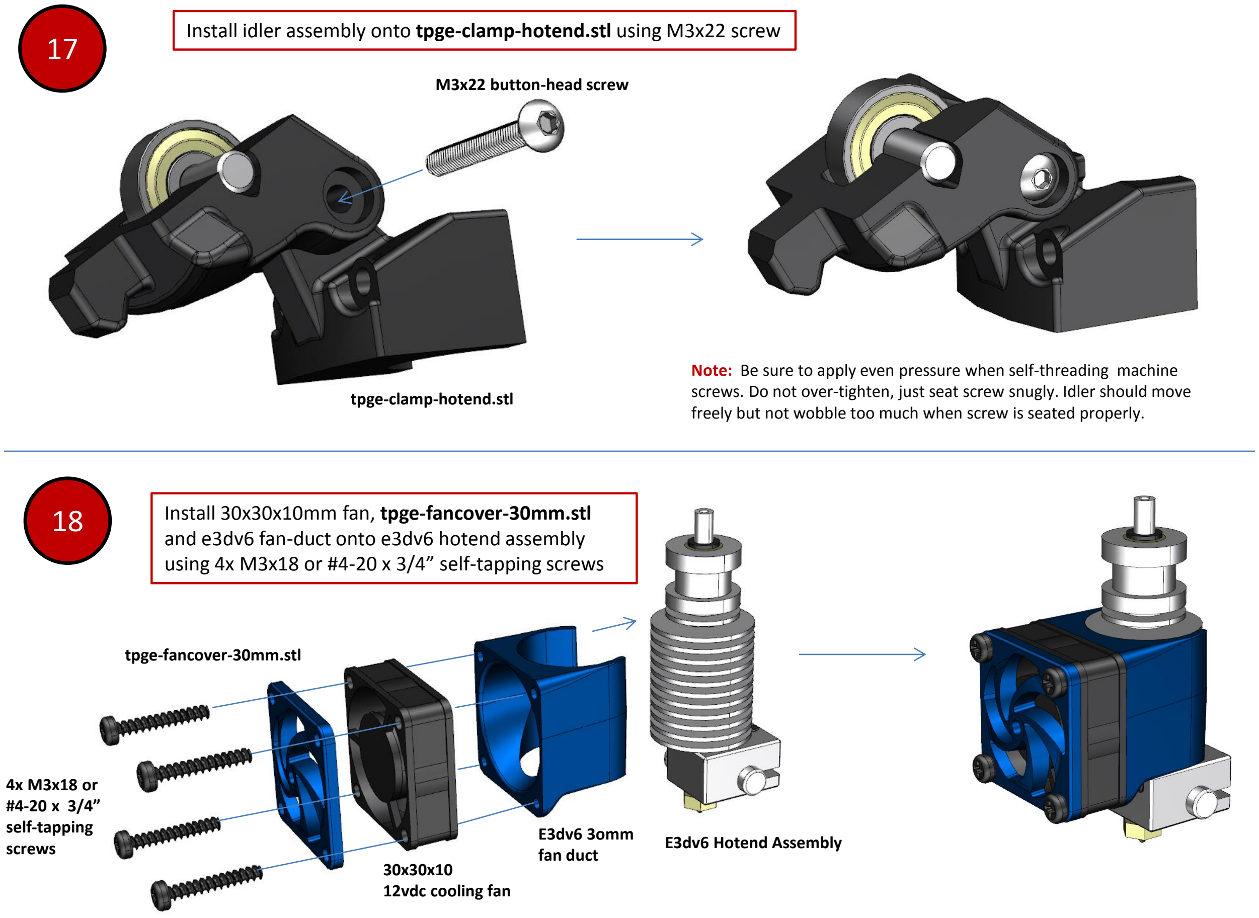
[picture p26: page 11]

17 | Install idler assembly onto tpge-clamp-hotend.stl using M3x22 screw

tpge-clamp-hotend.stl

Note: Be sure to apply even pressure when self-threading machine screws. Do not over-tighten, just seat screw snugly. Idler should move freely but not wobble too much when screw is seated properly.

18 | Install 30x30x10mm fan, tpge-fancover-30mm.stl and e3dv6 fan-duct onto e3dv6 hotend assembly using 4x M3x18 or #4-20 x 3/4” self-tapping screws

E3dv6 Hotend Assembly E3dv6 3omm fan duct
30x30x10
12vdc cooling fan

tpge-fancover-30mm.stl

4x M3x18 or
#4-20 x 3/4”

self-tapping
screws

M3x22 button-head screw

19

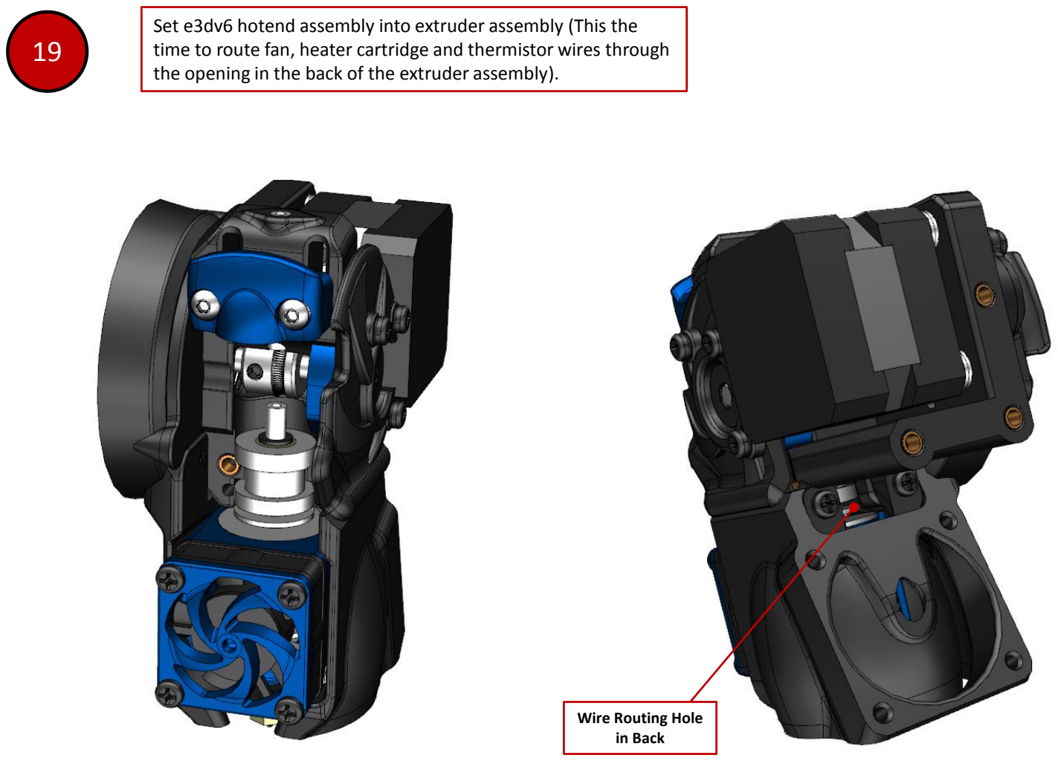
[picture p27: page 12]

### Set e3dv6 hotend assembly into extruder assembly (This the time to route fan, heater cartridge and thermistor wires through

the opening in the back of the extruder assembly).

Wire Routing Hole
in Back

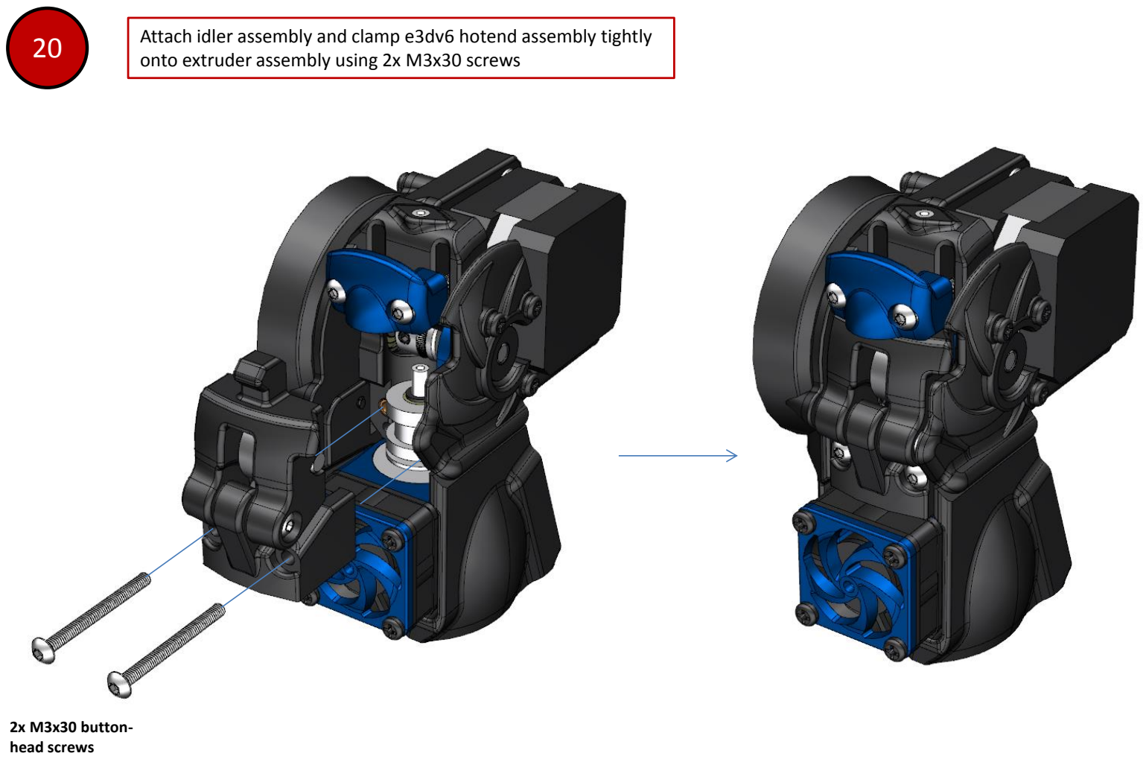
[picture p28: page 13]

20 | Attach idler assembly and clamp e3dv6 hotend assembly tightly onto extruder assembly using 2x M3x30 screws

2x M3x30 button-head screws

21

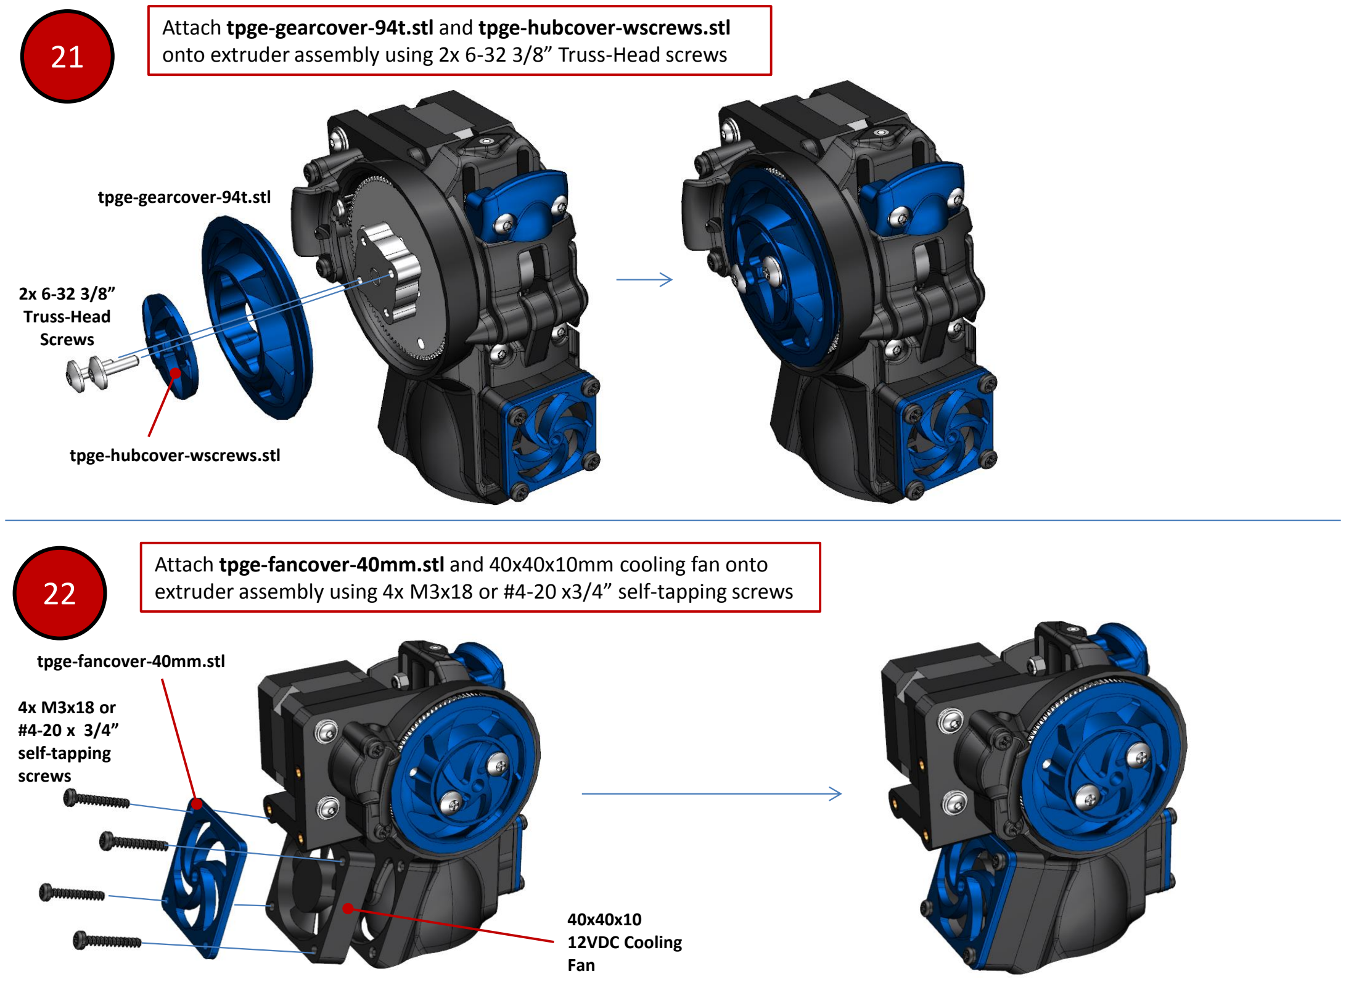
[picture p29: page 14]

### Attach tpge-gearcover-94t.stl and tpge-hubcover-wscrews.stl onto extruder assembly using 2x 6-32 3/8” Truss-Head screws

tpge-gearcover-94t.stl

tpge-hubcover-wscrews.stl

2x 6-32 3/8”
Truss-Head
Screws

22

### Attach tpge-fancover-40mm.stl and 40x40x10mm cooling fan onto extruder assembly using 4x M3x18 or #4-20 x3/4” self-tapping screws

tpge-fancover-40mm.stl

4x M3x18 or
#4-20 x 3/4”

self-tapping
screws

40x40x10
12VDC Cooling
Fan

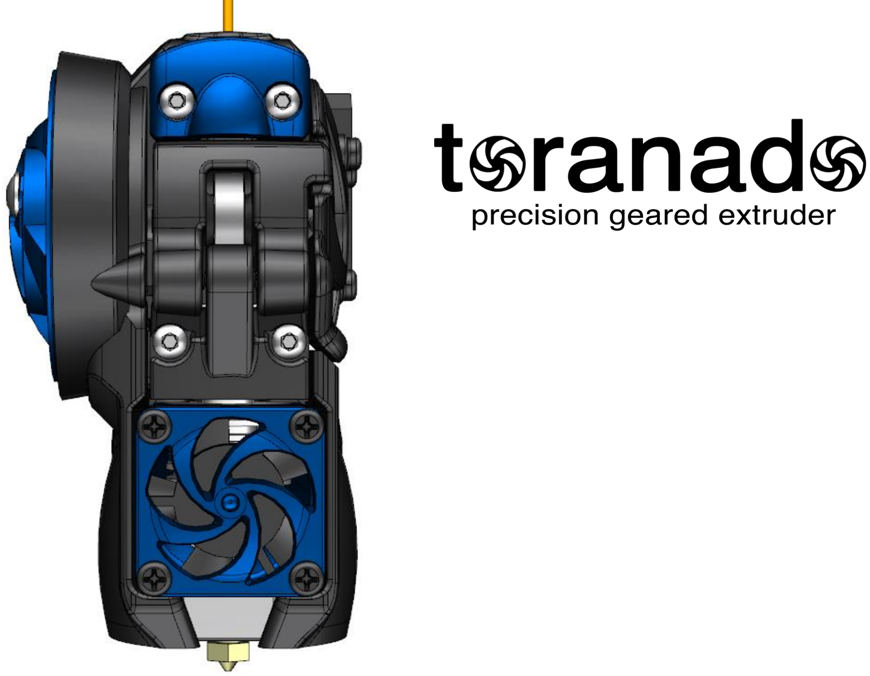
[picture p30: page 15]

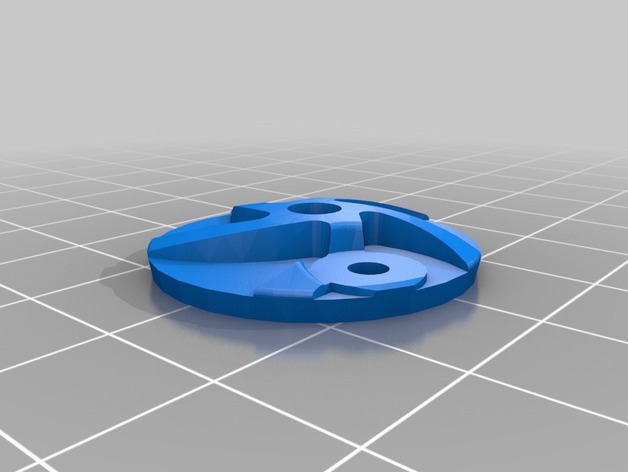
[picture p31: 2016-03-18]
Assembly/Sub-Assemblies/Muxed Assemblies/The_Toranado_Precision_Geared_1.75mm_Extruder/images/ba5476a4cd65d948d1e5d7d83cb9fd95_preview_featured.jpg

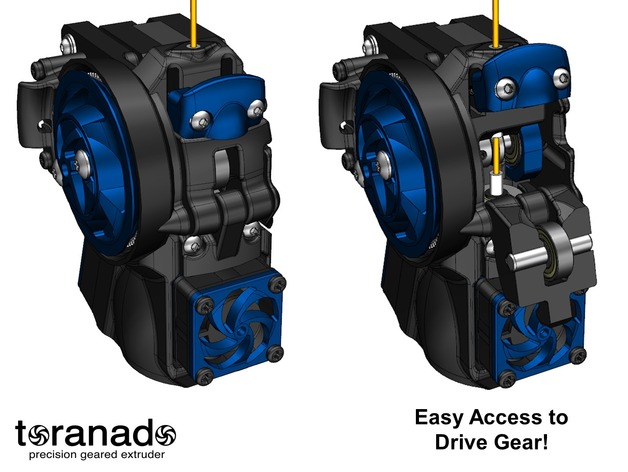
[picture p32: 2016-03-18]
Assembly/Sub-Assemblies/Muxed Assemblies/The_Toranado_Precision_Geared_1.75mm_Extruder/images/e882a307eb7f301215f229440f366e8c_preview_featured.jpg

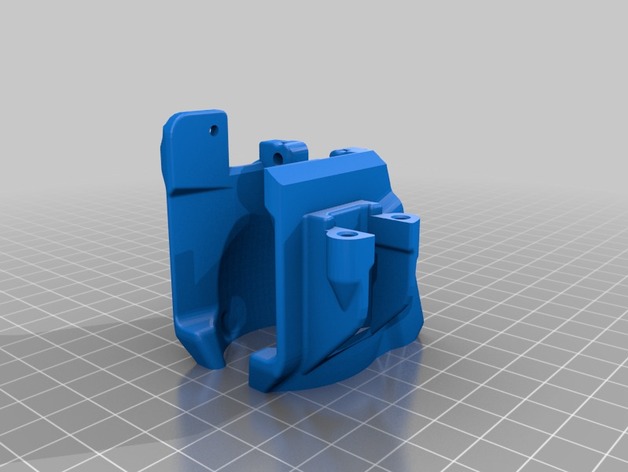
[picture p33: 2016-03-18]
Assembly/Sub-Assemblies/Muxed Assemblies/The_Toranado_Precision_Geared_1.75mm_Extruder/images/fd9245b678cd8bf5a20cb2c7eb5a2ed8_preview_featured.jpg

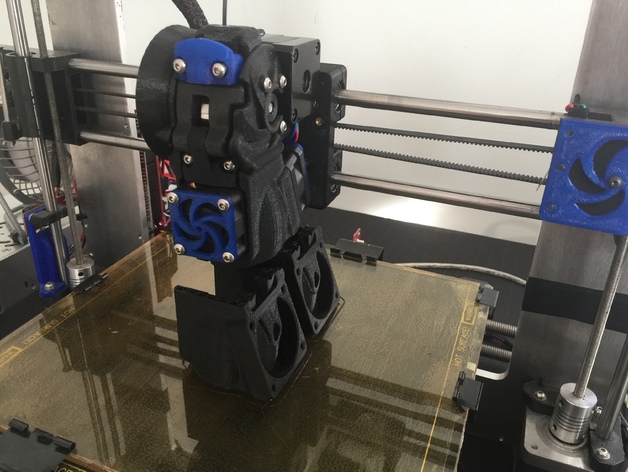
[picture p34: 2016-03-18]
Assembly/Sub-Assemblies/Muxed Assemblies/The_Toranado_Precision_Geared_1.75mm_Extruder/images/dfb6a3765175e9ed1e62de061d19aabe_preview_featured.JPG

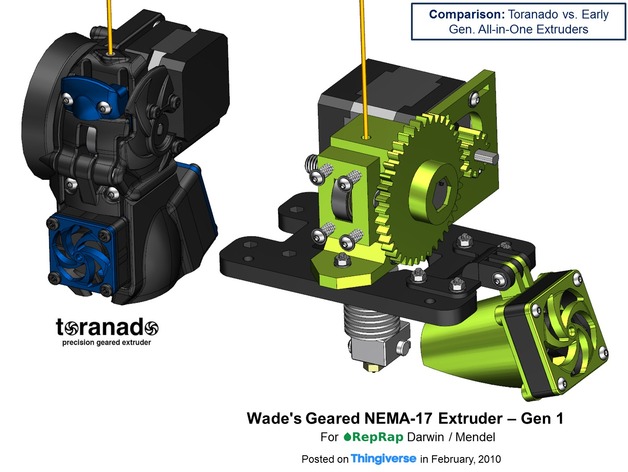
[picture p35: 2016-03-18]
Assembly/Sub-Assemblies/Muxed Assemblies/The_Toranado_Precision_Geared_1.75mm_Extruder/images/9050125f9d37b5bea642cd9987c7eac4_preview_featured.jpg

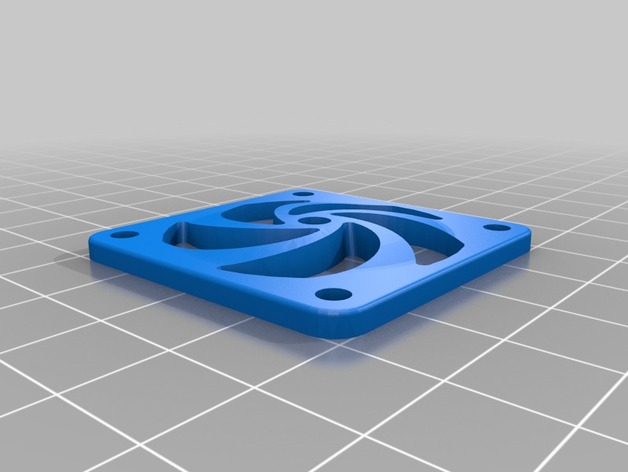
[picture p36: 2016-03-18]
Assembly/Sub-Assemblies/Muxed Assemblies/The_Toranado_Precision_Geared_1.75mm_Extruder/images/6fd530c8da6b0574d96c3b3ad818576f_preview_featured.jpg

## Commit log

2015-10-05 Initial Commit
    First upload of my changes to the system of jand1122 to Github
    [Angle_Bracket.FCStd, BOM.ods, Bearings.FCStd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]
2015-10-11 New Assembly
    Changed Folder Structure
    Changed too large distancer in Right Motor
    New Assembly with all parts, without constraints
    [Bearings.FCStd, Core(XY).step, Disctancers.FCStd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]
2015-10-12 Folders restructured
    Folders restructured for better overview and removal of duplicates
    [Angle_Bracket.FCStd, Bearings.FCStd, Bed214.FCStd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]
2015-10-14 Printhead
    E3D Printhead added
    [Extruder-blower-support.fcstd, Extruder-body.fcstd, Extruder-drive-gear.fcstd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]
2015-10-15 Belt Path optimised
    Moved Bearings of Motor Holders and Idlers 3mm towards Middle
    [GT2-Belt_left.FCStd, GT2-Belt_right.FCStd, GT2Bearing.FCStd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]
2015-10-17 Travel increased
    Started adding E3D Kraken Printhead. Increased travel in y-Direction
    for utilizing full printbed size with all four kraken nozzles.
    [Kraken.FCStd, Kraken_Carriage copy.FCStd, Kraken_Carriage.FCStd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]
2015-10-18 Parametric Cable Chain
    Added First Version of Parametric Cable Chain
    [CableChain.scad, text_on.scad]
2015-10-20 Starting y-Axis
    Started adding y-Axis.
    Added first 2 of 3 lead screws.
    [CableChain.scad, DIN912 - M4x15.FCStd, DIN912 - M4x20.FCStd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]
2015-10-20 Changed mounting of XY-Slide
    XY-Slide Bottom mounted instead of top mounted to allow for improved
    mounting.
    XY mounting hole has to be changed.
    [Floor.FCStd, GT2-Belt_right.FCStd, Subfloor.FCStd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]
2015-10-24 Motor Top Mount
    Repaired, Motor Mounts, XY-Slides and Idler Blocks for reversed mount
    of motors
    [DIN912 - M3x15.FCStd, DIN912 - M3x20.FCStd, DIN912 - M3x25.FCStd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]
2015-10-25 z-Axis beams pt. 3
    Third screw and beam for z-Axis added.
    [8mm flanged lead screw nut with 2mm thread.FCStd, DIN912 - M4x35.FCStd, DIN912 - M4x40.FCStd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]
2015-10-25 z-Axis Belt
    Belt added
    [GT2-Belt_Z.FCStd, Z-leadscrew-back-bearing-block.FCStd, z-Assmbly.FCStd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]
2015-11-25 New Input Project & Bugfixes
    Added Iteration 2 for future vertical carriage mount + Bugfix of
    carriages
    [0.4 nozzle.STEP, 0.4 nozzle2.STEP, 2020CornerPiece.fcstd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]
2016-03-18 Screws Replaced
    Replaced all screws with Fasteners Benchmark Version
    [30x30x10 12vdc cooling fan.FCStd, 40x40x10 12vdc cooling fan.FCStd, Acetal Main Gear.FCStd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]
2016-03-19 Prusa Hephestos Parts
    Copied Parts of Prusa Hephestos and start of repair of XY-System
    [Beltpiece.FCStd, Beltpiece.step, Toronade-Carrier-XY.FCStd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]
2016-03-19 Assembly2 Paths
    Repaired all Assembly2 Parts for Parts Updating
    [Knurl Nut.FCStd]
